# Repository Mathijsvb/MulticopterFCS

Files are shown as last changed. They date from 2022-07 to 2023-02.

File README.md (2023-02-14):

# About the project

MulticopterFCS is a flight controller build from the ground up. It is meant to be a development platform mainly focused on autonomous indoor flying of multi-rotor drones. 

> **Warning**
> The current version still contains design errors.

|Diagram|Board|
|---|---|
|DrawIO block diagrams-Pagina-5 drawio (3)|WhatsApp Image 2022-08-17 at 5 33 48 PM|

# Key features

**On board:**
* High performance MCU (STM32H743 running up to 480 MHz)
* Accelerometer and gyro (MPU6000)
* Magnetometer (HMC5883L)
* Pressure and temperature sensor (BMP388)
* 64-Kbit of F-RAM (FM24C64B)
* 2x RGB LED

**Connectors:**

| **quantity** 	| **purpose**  	| **connector type** 	| **Comment** |
|---	|---	|---	|---	|
| 1 	| SWD/JTAG 	| 1.27 mm pitch 10-pin 	| For programming and debugging 	|
| 1 	| SDIO 	| Micro SD Card 	| For logging data during the flight 	|
| 1 	| I²C 	| JST SH 4-pin 	| External I²C connector 	|
| 2 	| UART 	| JST SH 4-pin 	| External UART connector 	|
| 1 	| Battery  	| JST SH 2-pin 	| Used to measure battery voltage 	|
| 1 	| LED	  	| JST SH 8-pin 	| To control external LEDs 	|
| 1 	| IBUS 	| 2.54 mm pitch header 	| IBUS used by external receivers to communicate remote control signals |
| 6 	| PWM 	| 2.54 mm pitch header 	| PWM is used to control external ESC's 	|
| 1 	| Buzzer 	| 2.54 mm pitch header 	| For connecting a buzzer 	|
| 1 	| RPLiDAR  	| 2.50 mm MOLEX SPOX 7-pin 	| This connector will be used for the RPLiDAR 	|
| 2 	| USB 	| USB Mini B 	| USB1 goes directly to the MCU, USB2 gets converted to serial first 	|

# Roadmap:

1. ✔️ Project orientation
2. ✔️ Deciding on components
3. ✔️ Creating schematic
4. ✔️ Routing PCB
5. ✔️ Manufacturing the PCB
6.  Testing
	1. ✔️ Programming MCU
	2. ❌ Gyro/Accelerometer
		1.  ✔️ Find a the reason for to the Gyro/Accelerometer not working
		*   The MPU-6000 seems to need the ability to toggle CS which the current board does not support. Board revision is needed.
		2. Pick new Gyro/Accelerometer
	3. ❌ Magnetometer
		* Can't be detected with an I2C scanner, probably dead.
	4. Barometric pressure sensor
		1. ✔️ Check if it can be found with the I2C scanner.
		2. Check is values are sensible.
	5. ❌ On board F-RAM
		* Wrong IC choice on my part.
	6. ESC control
	7. IBUS communication
	8. Buzzer
	9. ✔️ LEDs
7. Writing drivers
	1. Gyro/Accelerometer
	2. Magnetometer
	3. Barometric pressure sensor
	4. On board F-RAM
	5. ESC control
	6. IBUS communication
	7. Buzzer and LEDs
	8. SD Card
	9. USB
8. Signal processing
	1. Data conversion and correction
	2. Data filtering
	3. Extended Kalman filter implementation for sensor fusion
	4. PI(D) controller
9. FSM controller 
10. Data logging on the SD Card

Future goals on the roadmap are likely to be Simultaneous Localization and Mapping using a LiDAR implementation. Based on this, autonomous indoor flight could be developed.

# Licensing

**This system is still a work in progress, use anything inside this repository at your own risk.**

This an open source project released under the BSD 3-Clause License.

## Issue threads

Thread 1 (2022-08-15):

Unable to communicate with the MPU6000

Mathijsvb, 2022-08-15:
The last few days I've been trying to communicate with the MPU6000 chip with no success. This chip functions as the acceleromiter and gyro of the flight controller board.

**What I've tried:**

1.  I've tried to communicate with the IC via SPI, but the MISO line remained low. I tried I²C, but no message was acknowledged.
2. I've tried replacing the IC with a new one. This yielded the same results. Do note that the chips did not arrive in their original packaging, so there is a chance that both IC's were reused and thus not as reliable.

---

**Additional info:**

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
This was recorded using a logic analyser. The first byte send starts with a 1 for MSB to indicate READ and follows with the register address 0x75 which should contain the WHO_AM_I register value which is 0x68 according to the datasheet. The figure shows nothing is returned. Attempting to read from other registers also returend nothing.
Clock frequency is 1 MHz, changing the frequency yields the same results. As for SPI settings: clock polarity is high and data is read on the second edge.

When looking at the board, the solder joints seem fine, but it is hard to judge since the joints are underneath the package.
Component values were checked and seemed fine.

Here is the schematic used. Signal lines go to the MCU unimpeded.
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

Any possible solutions or advice would be appreciated. Any feedback regarding the issue itself would also be nice, was it clear? Would you have liked additional info?

**References:**
General datasheet MPU6000: https://invensense.tdk.com/wp-content/uploads/2015/02/MPU-6000-Datasheet1.pdf
Register datasheet MPU6000: https://invensense.tdk.com/wp-content/uploads/2015/02/MPU-6000-Register-Map1.pdf
Datasheet of the MCU: https://www.st.com/resource/en/datasheet/stm32h743vi.pdf

Mathijsvb, 2022-08-18:
Update: Still no communication. What I did find was a [board that's build around MPU-6000](https://nl.rs-online.com/web/p/sensor-development-tools/8231892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) with most pins exposed. If I succeed in communicating with it, I can find out whether I'm did something wrong or if the IC's are dead.

---
At the same time, I'm looking for a suitable replacement for the MPU-6000 since it's discontinued. This is proving to be difficult since this type of IC is almost always out of stock. Some contenders:

* BNO055
* BMI088
* ISM330DHC
* LSM6DSOX
* MPU-6050 or ICM-20649 (These are discontinued as well but if availability is good they could still make sense)
* ICM-40609-D (currently in production but not yet available)

jurra, 2022-08-18:
Hi @Mathijsvb I can only give you feedback on the issue, is quite clear.

Jerzeek, 2022-08-24:
Yeah the MPU-6050 seems mostly pin compatible, but you do lose the ability for SPI communication, I don't know how important speed is. maybe pop in one of these 6050's and see if you can get i2c communication working. then you know if it is the board or the chip

Mathijsvb, 2022-08-29:
Hi @Jerzeek, thank you for the response. It's a good suggestion, and I would have been able to do this if I had not grounded the CS pin on the MPU-6000. This prevents being able to supply VLOGIC on the MPU-6050 (both pin 8 in the diagram). If I decide to use one of these, I'll definitely change this in a future revision of the board.

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

Mathijsvb, 2023-02-14:
I'm back with an update. Attaching the [MPU-6000 based dev board](https://nl.rs-online.com/web/p/sensor-development-tools/8231892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) discussed previously to the flight controller still yielded the same results of being unable to read out the WHO_AM_I register. So I took an entirely different microcontroller and attempted to read out the WHO_AM_I register again and it worked!

The difference between the two setups was that my test setup had a controllable CS pin, while the one in the flight controller was standard connected to ground. So what happens if we pull CS in the test setup standard low? Well, no response (and sometimes a gibberish response).

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

Searching around, it seems that some SPI devices need the CS transition to successfully manage communication and some don't. My best guess is that toggling CS is required for communication to remain in sync for the MPU-6000 (I was unable to find this detail in the datasheet, however). I'll close the issue for now.

This means a new board will need to be designed eventually after the other functionalities are tested.

Closed 2023-02-14.

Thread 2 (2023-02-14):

Improvements for the next board iteration

Mathijsvb, 2023-02-14:
In this issue, I'd like to compile all the known mistakes in the V1.0 board
1. No control over the MPU-6000 CS pin disallowing any form of communication over SPI (Or the ability to switch to I2C)
2. The FM24C64B works on 5V which I somehow completely missed and connected to the 3.3V supply

The future revision will contain:
1. A different gyro and accelerometer that is available

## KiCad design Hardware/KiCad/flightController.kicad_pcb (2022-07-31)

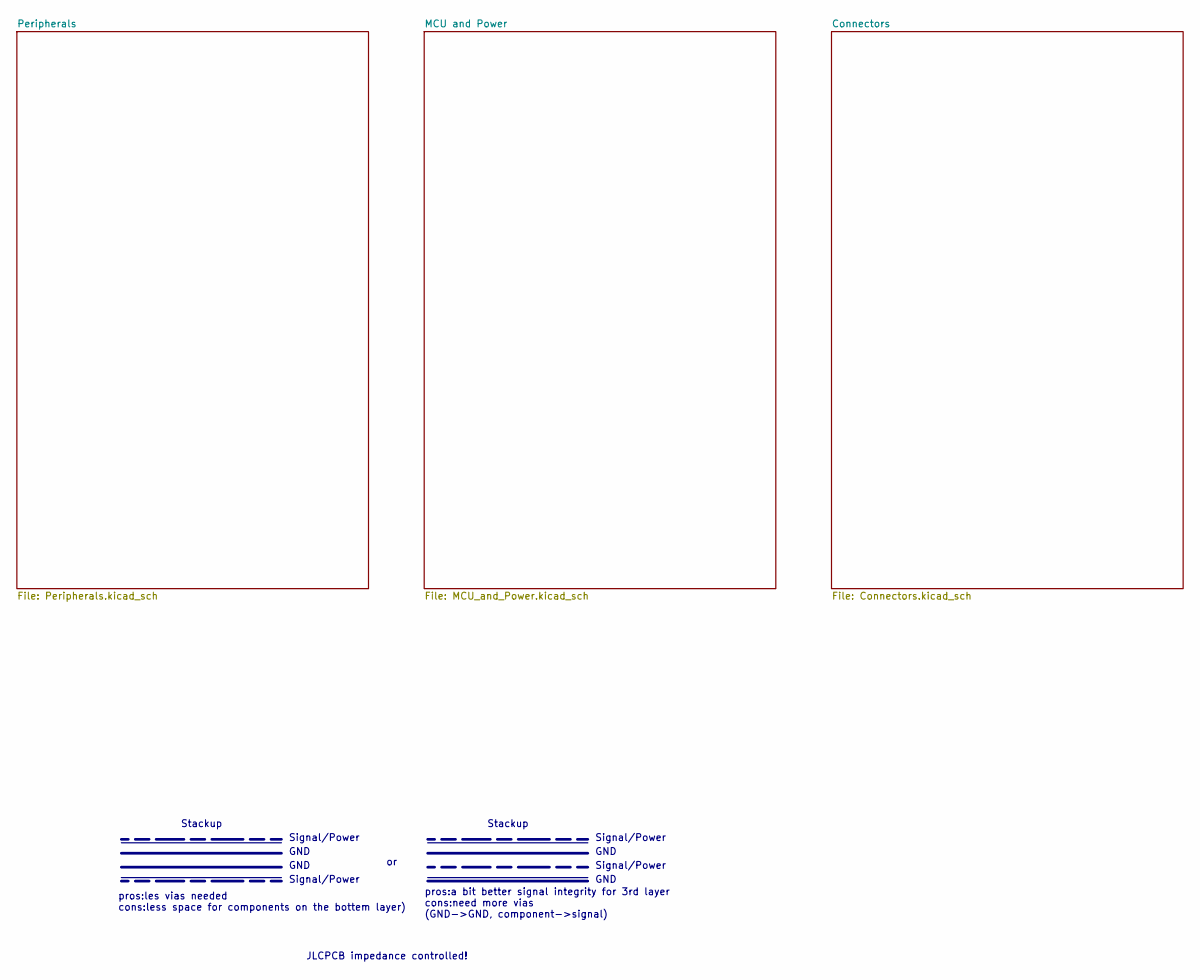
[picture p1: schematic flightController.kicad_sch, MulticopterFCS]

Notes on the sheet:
GND
Stackup
pros:les vias needed cons:less space for components on the bottem layer)
JLCPCB impedance controlled!
pros:a bit better signal integrity for 3rd layer cons:need more vias (GND->GND, component->signal)
Signal/Power

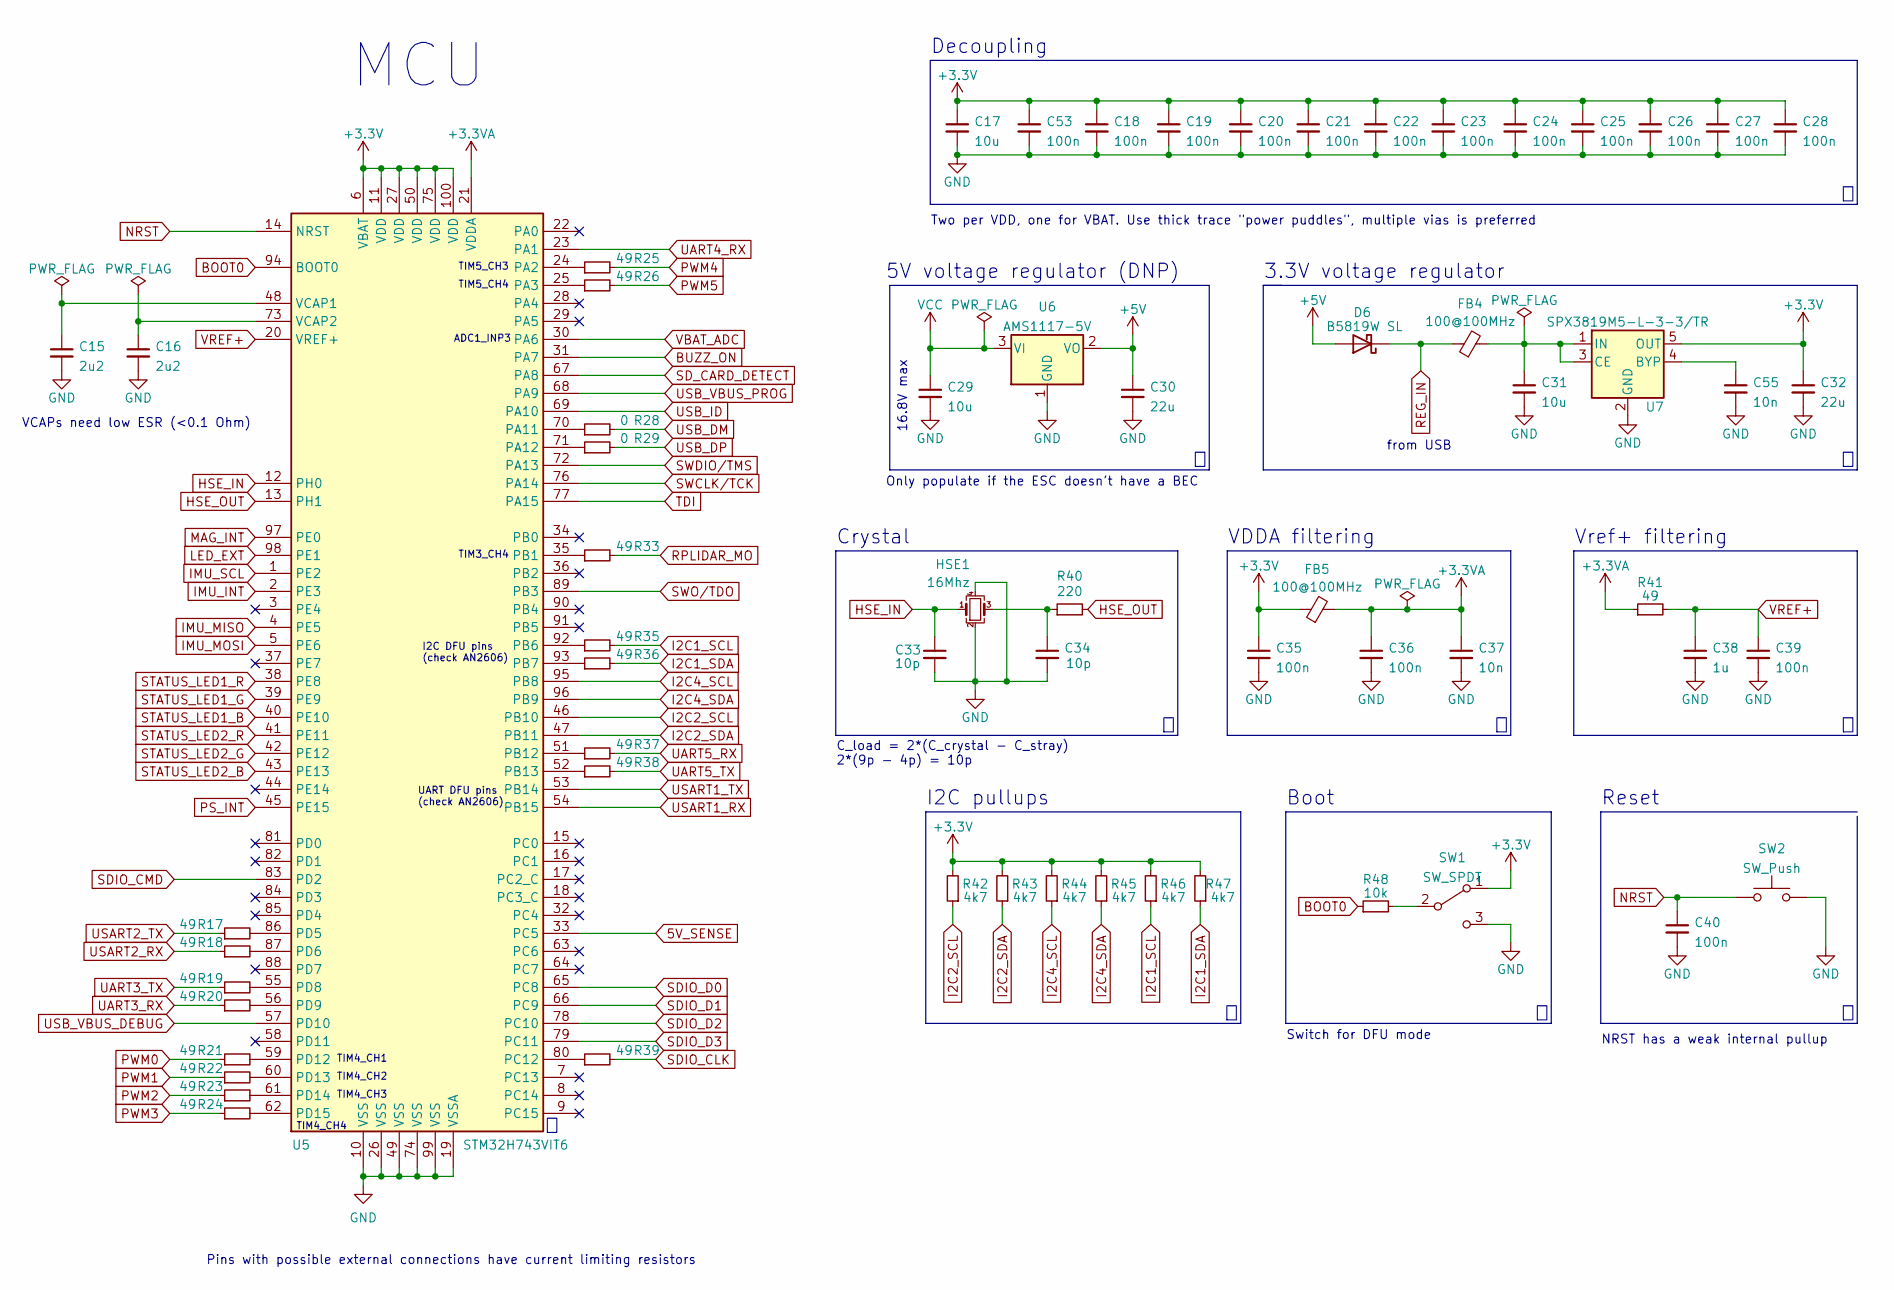
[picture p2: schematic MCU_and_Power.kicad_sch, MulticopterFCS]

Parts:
C15, C16: 2u2; C_0402_1005Metric; JLCPCB Part# C12530
C17, C29, C31: 10u; C_0603_1608Metric; JLCPCB Part# C96446
C18, C19, C20, C21, C22, C23, C24, C25, C26, C27, C28, C35, C36, C39, C40, C53: 100n; C_0402_1005Metric; JLCPCB Part# C1525
C30, C32: 22u; C_0603_1608Metric; JLCPCB Part# C59461
C33, C34: 10p; C_0402_1005Metric; JLCPCB Part# C32949
C37, C55: 10n; C_0402_1005Metric; JLCPCB Part# C15195
C38: 1u; C_0603_1608Metric; JLCPCB Part# C15849
D6: B5819W SL; D_SOD-123; JLCPCB Part# C8598
FB4, FB5: 100@100MHz; L_0603_1608Metric; JLCPCB Part# DNP
HSE1: 16Mhz; Crystal_SMD_3225-4Pin_3.2x2.5mm; JLCPCB Part# C13738
R17, R18, R19, R20, R21, R22, R23, R24, R25, R26, R33, R35, R36, R37, R38, R39, R41: 49; R_0402_1005Metric
R28, R29: 0; R_0402_1005Metric
R40: 220; R_0402_1005Metric
R42, R43, R44, R45, R46, R47: 4k7; R_0402_1005Metric
R48: 10k; R_0402_1005Metric
SW1: SW_SPDT; SW_SPDT_PCM12; JLCPCB Part# DNP
SW2: SW_Push; SW_SPST_FSMSM; JLCPCB Part# DNP
U5: STM32H743VIT6; LQFP-100_14x14mm_P0.5mm; JLCPCB Part# DNP
U6: AMS1117-5V; SOT-223-3_TabPin2; JLCPCB Part# DNP
U7: SPX3819M5-L-3-3/TR; SOT-23-5; JLCPCB Part# DNP

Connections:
5V_SENSE: U5.33 (PC5); also elsewhere on the board
+3.3VA: C36.1, C37.1, FB5.2, R41.1, U5.21 (VDDA)
+3V3: C17.1, C18.1, C19.1, C20.1, C21.1, C22.1, C23.1, C24.1, C25.1, C26.1, C27.1, C28.1, C32.1, C35.1, C53.1, FB5.1, R42.2, R43.2, R44.2, R45.2, R46.2, R47.2, SW1.1 (A), U5.6 (VBAT), U5.11 (VDD), U5.27 (VDD), U5.50 (VDD), U5.75 (VDD), U5.100 (VDD), U7.5 (OUT); also elsewhere on the board
+5V: C30.1, D6.2 (A), U6.2 (VO); also elsewhere on the board
BOOT0: R48.1, U5.94 (BOOT0)
BUZZ_ON: U5.31 (PA7); also elsewhere on the board
GND: C15.2, C16.2, C17.2, C18.2, C19.2, C20.2, C21.2, C22.2, C23.2, C24.2, C25.2, C26.2, C27.2, C28.2, C29.2, C30.2, C31.2, C32.2, C33.2, C34.2, C35.2, C36.2, C37.2, C38.2, C39.2, C40.2, C53.2, C55.2, HSE1.2, HSE1.4, SW1.3 (C), SW2.2, U5.10 (VSS), U5.19 (VSSA), U5.26 (VSS), U5.49 (VSS), U5.74 (VSS), U5.99 (VSS), U6.1 (GND), U7.2 (GND); also elsewhere on the board
HSE_IN: C33.1, HSE1.1, U5.12 (PH0)
HSE_OUT: R40.2, U5.13 (PH1)
I2C1_SCL: R35.2, R46.1; also elsewhere on the board
I2C1_SDA: R36.2, R47.1; also elsewhere on the board
I2C2_SCL: R42.1, U5.46 (PB10); also elsewhere on the board
I2C2_SDA: R43.1, U5.47 (PB11); also elsewhere on the board
I2C4_SCL: R44.1, U5.95 (PB8); also elsewhere on the board
I2C4_SDA: R45.1, U5.96 (PB9); also elsewhere on the board
IMU_INT: U5.2 (PE3); also elsewhere on the board
IMU_MISO: U5.4 (PE5); also elsewhere on the board
IMU_MOSI: U5.5 (PE6); also elsewhere on the board
IMU_SCL: U5.1 (PE2); also elsewhere on the board
LED_EXT: U5.98 (PE1); also elsewhere on the board
MAG_INT: U5.97 (PE0); also elsewhere on the board
NRST: C40.1, SW2.1, U5.14 (NRST); also elsewhere on the board
unnamed: C15.1, U5.48 (VCAP1)
unnamed: C16.1, U5.73 (VCAP2)
unnamed: C31.1, FB4.2, U7.1 (IN), U7.3 (CE)
unnamed: C34.1, HSE1.3, R40.1
unnamed: C55.1, U7.4 (BYP)
unnamed: R17.2, U5.86 (PD5)
unnamed: R18.2, U5.87 (PD6)
unnamed: R19.2, U5.55 (PD8)
unnamed: R20.2, U5.56 (PD9)
unnamed: R21.2, U5.59 (PD12)
unnamed: R22.2, U5.60 (PD13)
unnamed: R23.2, U5.61 (PD14)
unnamed: R24.2, U5.62 (PD15)
unnamed: R25.1, U5.24 (PA2)
unnamed: R26.1, U5.25 (PA3)
unnamed: R28.1, U5.70 (PA11)
unnamed: R29.1, U5.71 (PA12)
unnamed: R33.1, U5.35 (PB1)
unnamed: R35.1, U5.92 (PB6)
unnamed: R36.1, U5.93 (PB7)
unnamed: R37.1, U5.51 (PB12)
unnamed: R38.1, U5.52 (PB13)
unnamed: R39.1, U5.80 (PC12)
unnamed: R48.2, SW1.2 (B)
PS_INT: U5.45 (PE15); also elsewhere on the board
PWM0: R21.1; also elsewhere on the board
PWM1: R22.1; also elsewhere on the board
PWM2: R23.1; also elsewhere on the board
PWM3: R24.1; also elsewhere on the board
PWM4: R25.2; also elsewhere on the board
PWM5: R26.2; also elsewhere on the board
REG_IN: D6.1 (K), FB4.1; also elsewhere on the board
RPLIDAR_MO: R33.2; also elsewhere on the board
SDIO_CLK: R39.2; also elsewhere on the board
SDIO_CMD: U5.83 (PD2); also elsewhere on the board
SDIO_D0: U5.65 (PC8); also elsewhere on the board
SDIO_D1: U5.66 (PC9); also elsewhere on the board
SDIO_D2: U5.78 (PC10); also elsewhere on the board
SDIO_D3: U5.79 (PC11); also elsewhere on the board
SD_CARD_DETECT: U5.67 (PA8); also elsewhere on the board
STATUS_LED1_B: U5.40 (PE10); also elsewhere on the board
STATUS_LED1_G: U5.39 (PE9); also elsewhere on the board
STATUS_LED1_R: U5.38 (PE8); also elsewhere on the board
STATUS_LED2_B: U5.43 (PE13); also elsewhere on the board
STATUS_LED2_G: U5.42 (PE12); also elsewhere on the board
STATUS_LED2_R: U5.41 (PE11); also elsewhere on the board
SWCLK/TCK: U5.76 (PA14); also elsewhere on the board
SWDIO/TMS: U5.72 (PA13); also elsewhere on the board
SWO/TDO: U5.89 (PB3); also elsewhere on the board
TDI: U5.77 (PA15); also elsewhere on the board
UART3_RX: R20.1; also elsewhere on the board
UART3_TX: R19.1; also elsewhere on the board
UART4_RX: U5.23 (PA1); also elsewhere on the board
UART5_RX: R37.2; also elsewhere on the board
UART5_TX: R38.2; also elsewhere on the board
USART1_RX: U5.54 (PB15); also elsewhere on the board
USART1_TX: U5.53 (PB14); also elsewhere on the board
USART2_RX: R18.1; also elsewhere on the board
USART2_TX: R17.1; also elsewhere on the board
USB_DM: R28.2; also elsewhere on the board
USB_DP: R29.2; also elsewhere on the board
USB_ID: U5.69 (PA10); also elsewhere on the board
USB_VBUS_DEBUG: U5.57 (PD10); also elsewhere on the board
USB_VBUS_PROG: U5.68 (PA9); also elsewhere on the board
VBAT_ADC: U5.30 (PA6); also elsewhere on the board
VCC: C29.1, U6.3 (VI); also elsewhere on the board
VREF+: C38.1, C39.1, R41.2, U5.20 (VREF+)

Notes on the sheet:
Boot
Reset
ADC1_INP3
TIM5_CH3
from USB
3.3V voltage regulator
TIM4_CH3
Vref+ filtering
Pins with possible external connections have current limiting resistors
5V voltage regulator (DNP)
UART DFU pins (check AN2606)
VCAPs need low ESR (<0.1 Ohm)
VDDA filtering
Decoupling
16.8V max
I2C pullups
TIM4_CH4
NRST has a weak internal pullup
Crystal
TIM4_CH2
TIM4_CH1
MCU
Two per VDD, one for VBAT. Use thick trace "power puddles", multiple vias is preferred
I2C DFU pins (check AN2606)
Switch for DFU mode
TIM5_CH4
Only populate if the ESC doesn't have a BEC
C_load = 2*(C_crystal - C_stray) 2*(9p - 4p) = 10p
TIM3_CH4

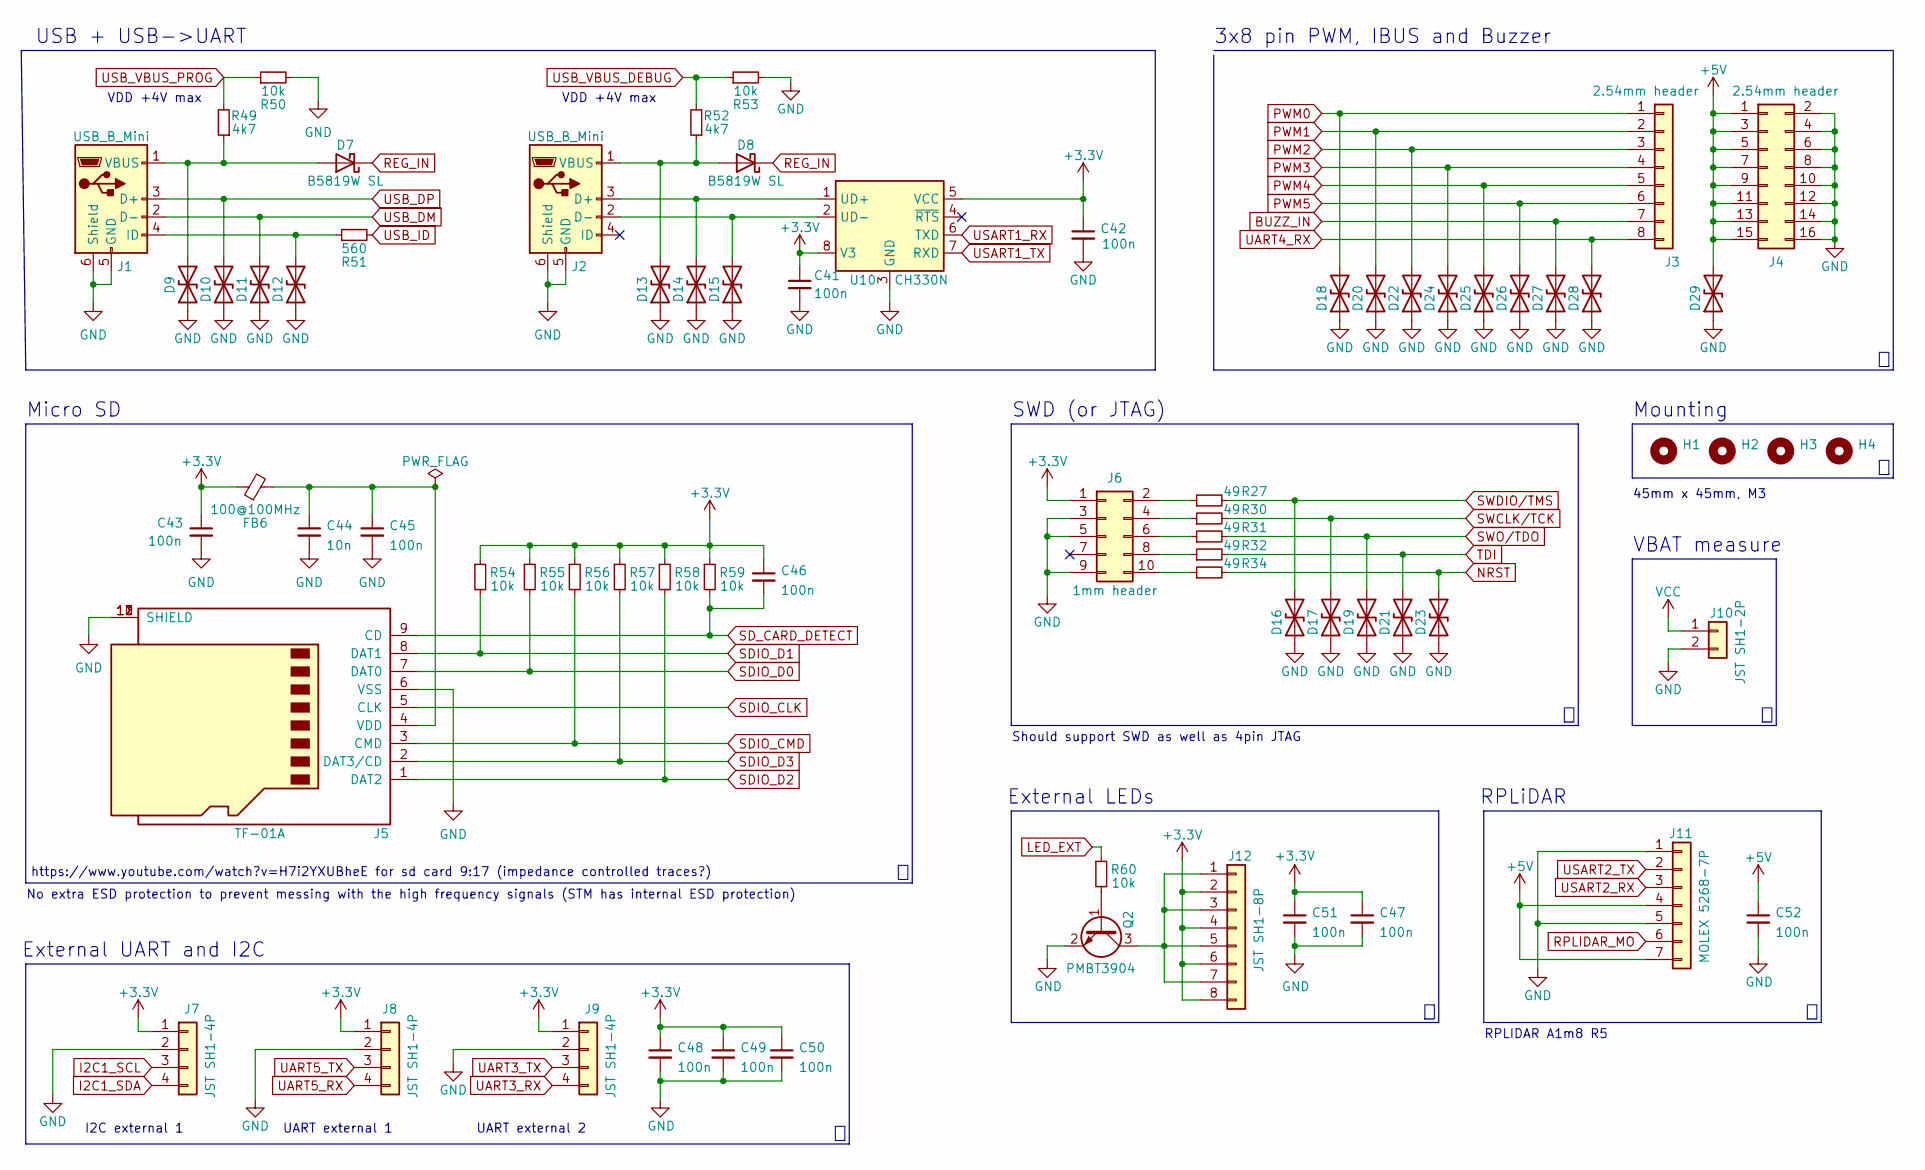
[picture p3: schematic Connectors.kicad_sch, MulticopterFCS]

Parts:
C41, C42, C43, C45, C46, C47, C48, C49, C50, C51, C52: 100n; C_0402_1005Metric; JLCPCB Part# C1525
C44: 10n; C_0402_1005Metric; JLCPCB Part# C15195
D7, D8: B5819W SL; D_SOD-123; JLCPCB Part# C8598
D9, D10, D11, D12, D13, D14, D15, D16, D17, D18, D19, D20, D21, D22, D23, D24, D25, D26, D27, D28, D29: LXES15AAA1-133; R_0402_1005Metric
FB6: 100@100MHz; L_0603_1608Metric; JLCPCB Part# DNP
H1, H2, H3, H4: MountingHole; MountingHole_3.2mm_M3_ISO14580_Pad; JLCPCB Part# DNP
J1, J2: USB_B_Mini; USB_Mini-B_Wuerth_65100516121_Horizontal; JLCPCB Part# DNP
J3: 2.54mm header; PinHeader_1x08_P2.54mm_Vertical_lessSilk; JLCPCB Part# DNP
J4: 2.54mm header; PinHeader_2x08_P2.54mm_Horizontal_lessSilk; JLCPCB Part# DNP
J5: TF-01A; JLCPCB Part# DNP
J6: 1mm header; PinHeader_2x05_P1.27mm_Vertical_SMD; JLCPCB Part# DNP
J7, J8, J9: JST SH1-4P; JST_SH_SM04B-SRSS-TB_1x04-1MP_P1.00mm_Horizontal; JLCPCB Part# DNP
J10: JST SH1-2P; JST_SHL_SM02B-SHLS-TF_1x02-1MP_P1.00mm_Horizontal; JLCPCB Part# DNP
J11: MOLEX 5268-7P; Molex_SPOX_5268-07A_1x07_P2.50mm_Horizontal; JLCPCB Part# DNP
J12: JST SH1-8P; JST_SH_SM08B-SRSS-TB_1x08-1MP_P1.00mm_Horizontal; JLCPCB Part# DNP
Q2: PMBT3904; SOT-23; JLCPCB Part# DNP
R27, R30, R31, R32, R34: 49; R_0402_1005Metric
R49, R52: 4k7; R_0402_1005Metric
R50, R53, R54, R55, R56, R57, R58, R59, R60: 10k; R_0402_1005Metric
R51: 560; R_0402_1005Metric
U10: CH330N; SOP-8_3.9x4.9mm_P1.27mm; JLCPCB Part# C108996

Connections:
+3V3: C41.1, C42.1, C43.1, C46.1, C47.1, C48.1, C49.1, C50.1, C51.1, FB6.1, J6.1, J7.1, J8.1, J9.1, J12.2, J12.4, J12.6, J12.8, R54.1, R55.1, R56.1, R57.1, R58.1, R59.1, U10.5 (VCC), U10.8 (V3); also elsewhere on the board
+5V: C52.1, D29.2 (A2), J4.1, J4.3, J4.5, J4.7, J4.9, J4.11, J4.13, J4.15, J11.4, J11.7; also elsewhere on the board
BUZZ_IN: D27.2 (A2), J3.7; also elsewhere on the board
GND: C41.2, C42.2, C43.2, C44.2, C45.2, C47.2, C48.2, C49.2, C50.2, C51.2, C52.2, D9.1 (A1), D10.1 (A1), D11.1 (A1), D12.1 (A1), D13.1 (A1), D14.1 (A1), D15.1 (A1), D16.1 (A1), D17.1 (A1), D18.1 (A1), D19.1 (A1), D20.1 (A1), D21.1 (A1), D22.1 (A1), D23.1 (A1), D24.1 (A1), D25.1 (A1), D26.1 (A1), D27.1 (A1), D28.1 (A1), D29.1 (A1), J1.5 (GND), J1.6 (Shield), J2.5 (GND), J2.6 (Shield), J4.2, J4.4, J4.6, J4.8, J4.10, J4.12, J4.14, J4.16, J5.6 (VSS), J5.10 (SHIELD), J5.11 (SHIELD), J5.12 (SHIELD), J5.13 (SHIELD), J6.3, J6.5, J6.9, J7.2, J8.2, J9.2, J10.2, J11.1, J11.5, Q2.2 (E), R50.2, R53.2, U10.3 (GND); also elsewhere on the board
I2C1_SCL: J7.3; also elsewhere on the board
I2C1_SDA: J7.4; also elsewhere on the board
LED_EXT: R60.1; also elsewhere on the board
NRST: D23.2 (A2), R34.2; also elsewhere on the board
unnamed: C44.1, C45.1, FB6.2, J5.4 (VDD)
unnamed: D7.2 (A), D9.2 (A2), J1.1 (VBUS), R49.1
unnamed: D8.2 (A), D13.2 (A2), J2.1 (VBUS), R52.1
unnamed: D12.2 (A2), J1.4 (ID), R51.1
unnamed: D15.2 (A2), J2.2 (D-), U10.2 (UD-)
unnamed: D14.2 (A2), J2.3 (D+), U10.1 (UD+)
unnamed: J6.2, R27.1
unnamed: J6.4, R30.1
unnamed: J6.6, R31.1
unnamed: J6.8, R32.1
unnamed: J6.10, R34.1
unnamed: J12.1, J12.3, J12.5, J12.7, Q2.3 (C)
unnamed: Q2.1 (B), R60.2
PWM0: D18.2 (A2), J3.1; also elsewhere on the board
PWM1: D20.2 (A2), J3.2; also elsewhere on the board
PWM2: D22.2 (A2), J3.3; also elsewhere on the board
PWM3: D24.2 (A2), J3.4; also elsewhere on the board
PWM4: D25.2 (A2), J3.5; also elsewhere on the board
PWM5: D26.2 (A2), J3.6; also elsewhere on the board
REG_IN: D7.1 (K), D8.1 (K); also elsewhere on the board
RPLIDAR_MO: J11.6; also elsewhere on the board
SDIO_CLK: J5.5 (CLK); also elsewhere on the board
SDIO_CMD: J5.3 (CMD), R56.2; also elsewhere on the board
SDIO_D0: J5.7 (DAT0), R55.2; also elsewhere on the board
SDIO_D1: J5.8 (DAT1), R54.2; also elsewhere on the board
SDIO_D2: J5.1 (DAT2), R58.2; also elsewhere on the board
SDIO_D3: J5.2 (DAT3/CD), R57.2; also elsewhere on the board
SD_CARD_DETECT: C46.2, J5.9 (CD), R59.2; also elsewhere on the board
SWCLK/TCK: D17.2 (A2), R30.2; also elsewhere on the board
SWDIO/TMS: D16.2 (A2), R27.2; also elsewhere on the board
SWO/TDO: D19.2 (A2), R31.2; also elsewhere on the board
TDI: D21.2 (A2), R32.2; also elsewhere on the board
UART3_RX: J9.4; also elsewhere on the board
UART3_TX: J9.3; also elsewhere on the board
UART4_RX: D28.2 (A2), J3.8; also elsewhere on the board
UART5_RX: J8.4; also elsewhere on the board
UART5_TX: J8.3; also elsewhere on the board
USART1_RX: U10.6 (TXD); also elsewhere on the board
USART1_TX: U10.7 (RXD); also elsewhere on the board
USART2_RX: J11.3; also elsewhere on the board
USART2_TX: J11.2; also elsewhere on the board
USB_DM: D11.2 (A2), J1.2 (D-); also elsewhere on the board
USB_DP: D10.2 (A2), J1.3 (D+); also elsewhere on the board
USB_ID: R51.2; also elsewhere on the board
USB_VBUS_DEBUG: R52.2, R53.1; also elsewhere on the board
USB_VBUS_PROG: R49.2, R50.1; also elsewhere on the board
VCC: J10.1; also elsewhere on the board

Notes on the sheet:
https://www.youtube.com/watch?v=H7i2YXUBheE for sd card 9:17 (impedance controlled traces?)
RPLiDAR
Mounting
External LEDs
UART external 2
External UART and I2C
Micro SD
VDD +4V max
3x8 pin PWM, IBUS and Buzzer
No extra ESD protection to prevent messing with the high frequency signals (STM has internal ESD protection)
I2C external 1
45mm x 45mm, M3
RPLIDAR A1m8 R5
Should support SWD as well as 4pin JTAG
VBAT measure
SWD (or JTAG)
USB + USB->UART
UART external 1

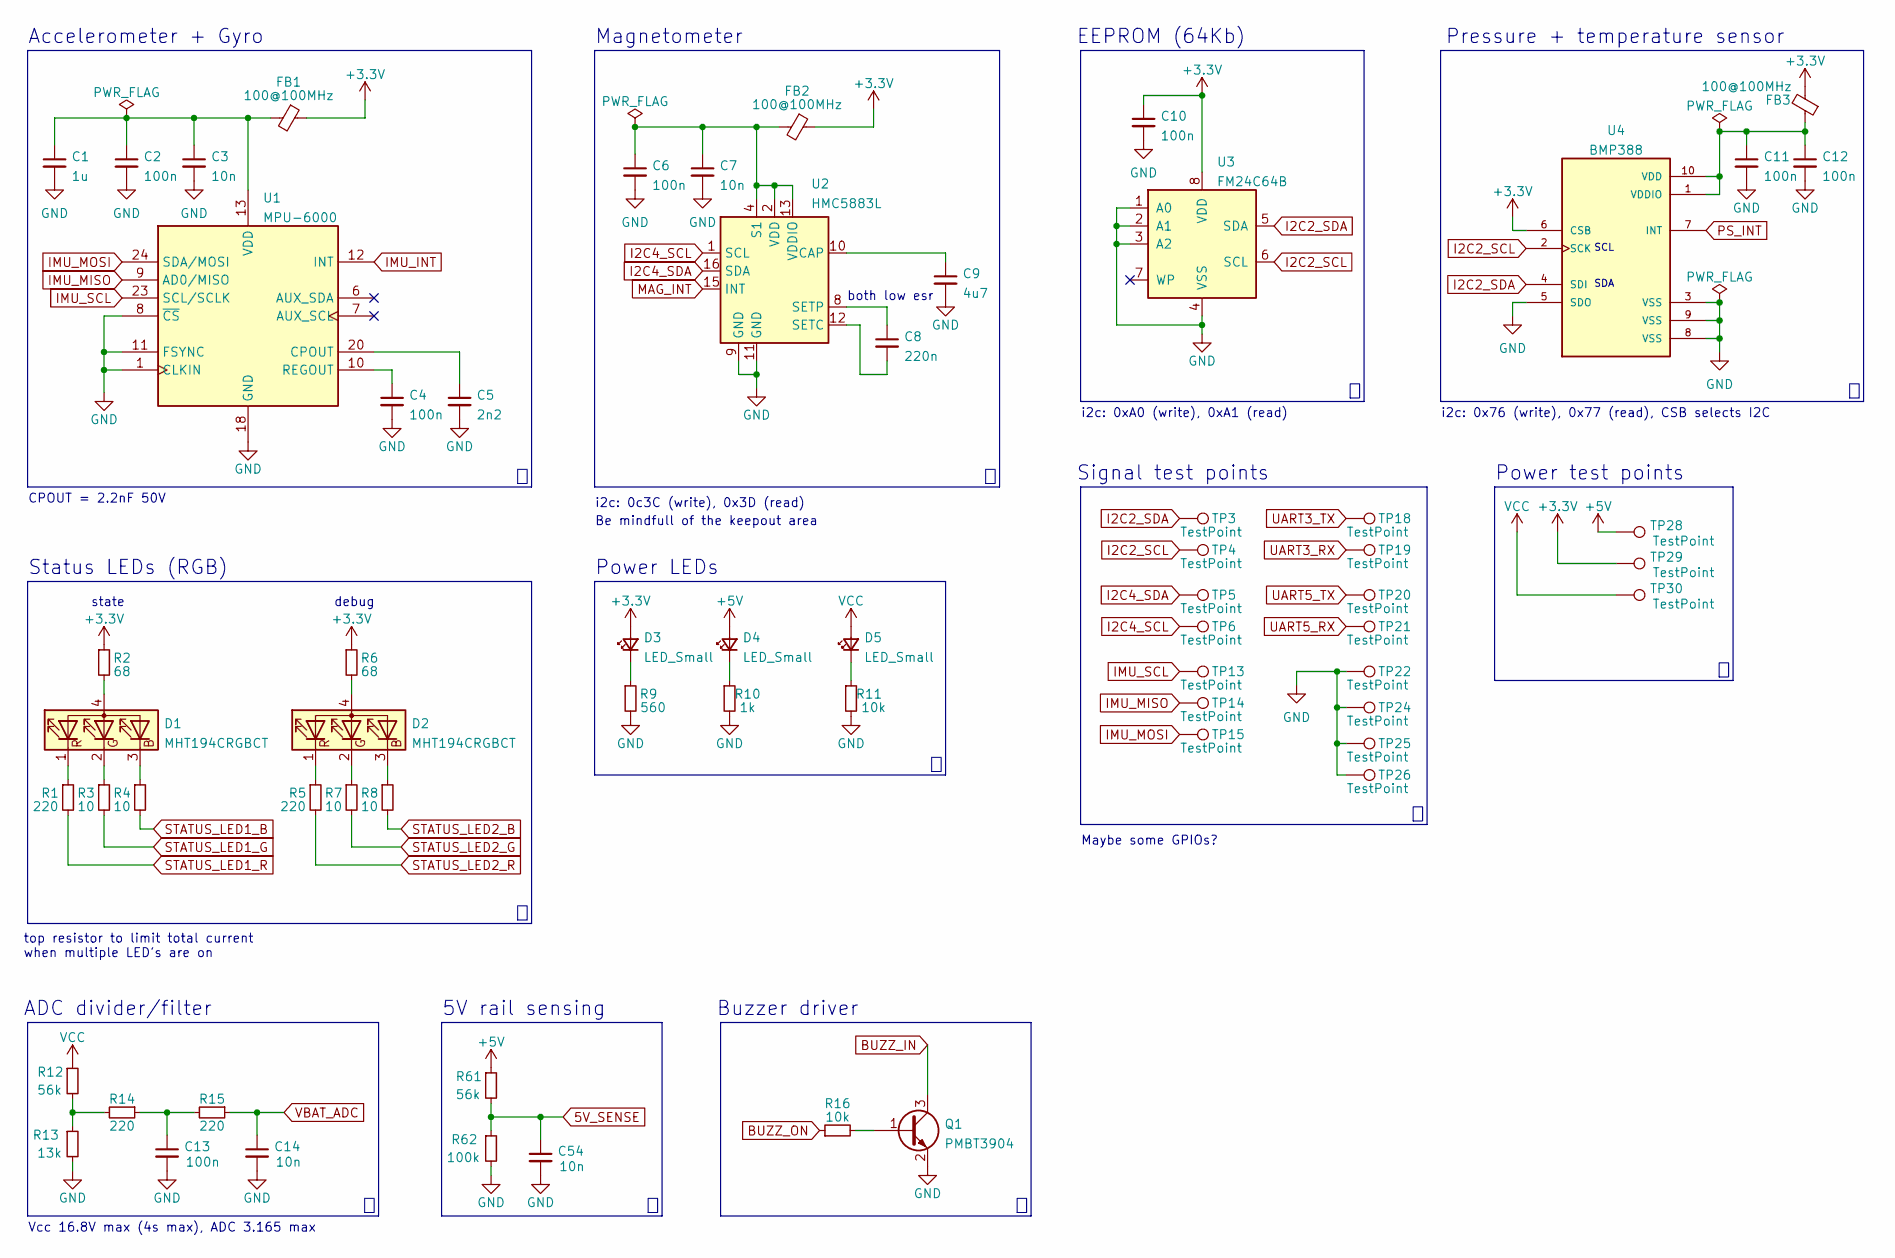
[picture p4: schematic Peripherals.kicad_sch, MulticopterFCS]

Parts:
C1: 1u; C_0603_1608Metric; JLCPCB Part# C15849
C2, C4, C6, C10, C11, C12, C13: 100n; C_0402_1005Metric; JLCPCB Part# C1525
C3, C7, C14, C54: 10n; C_0402_1005Metric; JLCPCB Part# C15195
C5: 2n2; C_0402_1005Metric; JLCPCB Part# C1531
C8: 220n; C_0603_1608Metric; JLCPCB Part# C21120
C9: 4u7; C_0603_1608Metric; JLCPCB Part# C19666
D1, D2: MHT194CRGBCT; 0605; JLCPCB Part# DNP
D3, D4, D5: LED_Small; LED_0603_1608Metric; JLCPCB Part# DNP
FB1, FB2, FB3: 100@100MHz; L_0603_1608Metric; JLCPCB Part# DNP
Q1: PMBT3904; SOT-23; JLCPCB Part# DNP
R1, R5, R14, R15: 220; R_0402_1005Metric
R2, R6: 68; R_0603_1608Metric
R3, R4, R7, R8: 10; R_0402_1005Metric
R9: 560; R_0603_1608Metric
R10: 1k; R_0603_1608Metric
R11: 10k; R_0603_1608Metric
R12, R61: 56k; R_0402_1005Metric
R13: 13k; R_0402_1005Metric
R16: 10k; R_0402_1005Metric
R62: 100k; R_0402_1005Metric
TP3, TP4, TP5, TP6, TP13, TP14, TP15, TP18, TP19, TP20, TP21, TP22, TP24, TP25, TP26, TP28, TP29, TP30: TestPoint; TestPoint_Pad_D1.0mm; JLCPCB Part# DNP
U1: MPU-6000; InvenSense_QFN-24_4x4mm_P0.5mm; JLCPCB Part# DNP
U2: HMC5883L; LGA-16_3x3mm_P0.5mm_Large_Pads; JLCPCB Part# DNP
U3: FM24C64B; SOIC-8_3.9x4.9mm_P1.27mm; JLCPCB Part# DNP
U4: BMP388; PQFN50P200X200X80-10N; JLCPCB Part# C779278

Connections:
5V_SENSE: C54.1, R61.2, R62.1; also elsewhere on the board
+3V3: C10.1, D3.2 (A), FB1.1, FB2.1, FB3.2, R2.1, R6.1, TP29.1, U3.8 (VDD), U4.6 (CSB); also elsewhere on the board
+5V: D4.2 (A), R61.1, TP28.1; also elsewhere on the board
BUZZ_IN: Q1.3 (C); also elsewhere on the board
BUZZ_ON: R16.1; also elsewhere on the board
GND: C1.2, C2.2, C3.2, C4.2, C5.2, C6.2, C7.2, C9.2, C10.2, C11.2, C12.2, C13.2, C14.2, C54.2, Q1.2 (E), R9.2, R10.2, R11.2, R13.2, R62.2, TP22.1, TP24.1, TP25.1, TP26.1, U1.1 (CLKIN), U1.8 (~CS), U1.11 (FSYNC), U1.18 (GND), U2.9 (GND), U2.11 (GND), U3.1 (A0), U3.2 (A1), U3.3 (A2), U3.4 (VSS), U4.3 (VSS), U4.5 (SDO), U4.8 (VSS), U4.9 (VSS); also elsewhere on the board
I2C2_SCL: TP4.1, U3.6 (SCL), U4.2 (SCK); also elsewhere on the board
I2C2_SDA: TP3.1, U3.5 (SDA), U4.4 (SDI); also elsewhere on the board
I2C4_SCL: TP6.1, U2.1 (SCL); also elsewhere on the board
I2C4_SDA: TP5.1, U2.16 (SDA); also elsewhere on the board
IMU_INT: U1.12 (INT); also elsewhere on the board
IMU_MISO: TP14.1, U1.9 (AD0/MISO); also elsewhere on the board
IMU_MOSI: TP15.1, U1.24 (SDA/MOSI); also elsewhere on the board
IMU_SCL: TP13.1, U1.23 (SCL/SCLK); also elsewhere on the board
MAG_INT: U2.15 (INT); also elsewhere on the board
unnamed: C1.1, C2.1, C3.1, FB1.2, U1.13 (VDD)
unnamed: C4.1, U1.10 (REGOUT)
unnamed: C5.1, U1.20 (CPOUT)
unnamed: C6.1, C7.1, FB2.2, U2.2 (VDD), U2.4 (S1), U2.13 (VDDIO)
unnamed: C8.1, U2.8 (SETP)
unnamed: C8.2, U2.12 (SETC)
unnamed: C9.1, U2.10 (CAP)
unnamed: C11.1, C12.1, FB3.1, U4.1 (VDDIO), U4.10 (VDD)
unnamed: C13.1, R14.1, R15.2
unnamed: D1.1 (RK), R1.1
unnamed: D1.2 (GK), R3.1
unnamed: D1.3 (BK), R4.1
unnamed: D1.4 (A), R2.2
unnamed: D2.1 (RK), R5.1
unnamed: D2.2 (GK), R7.1
unnamed: D2.3 (BK), R8.1
unnamed: D2.4 (A), R6.2
unnamed: D3.1 (K), R9.1
unnamed: D4.1 (K), R10.1
unnamed: D5.1 (K), R11.1
unnamed: Q1.1 (B), R16.2
unnamed: R12.2, R13.1, R14.2
PS_INT: U4.7 (INT); also elsewhere on the board
STATUS_LED1_B: R4.2; also elsewhere on the board
STATUS_LED1_G: R3.2; also elsewhere on the board
STATUS_LED1_R: R1.2; also elsewhere on the board
STATUS_LED2_B: R8.2; also elsewhere on the board
STATUS_LED2_G: R7.2; also elsewhere on the board
STATUS_LED2_R: R5.2; also elsewhere on the board
UART3_RX: TP19.1; also elsewhere on the board
UART3_TX: TP18.1; also elsewhere on the board
UART5_RX: TP21.1; also elsewhere on the board
UART5_TX: TP20.1; also elsewhere on the board
VBAT_ADC: C14.1, R15.1; also elsewhere on the board
VCC: D5.2 (A), R12.1, TP30.1; also elsewhere on the board

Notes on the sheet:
SCL
ADC divider/filter
5V rail sensing
Signal test points
Buzzer driver
top resistor to limit total current when multiple LED's are on
Power LEDs
Maybe some GPIOs?
i2c: 0x76 (write), 0x77 (read), CSB selects I2C
Magnetometer
SDA
both low esr
EEPROM (64Kb)
i2c: 0c3C (write), 0x3D (read)
debug
i2c: 0xA0 (write), 0xA1 (read)
CPOUT = 2.2nF 50V
Pressure + temperature sensor
Be mindfull of the keepout area
Status LEDs (RGB)
Accelerometer + Gyro
Vcc 16.8V max (4s max), ADC 3.165 max
Power test points
state

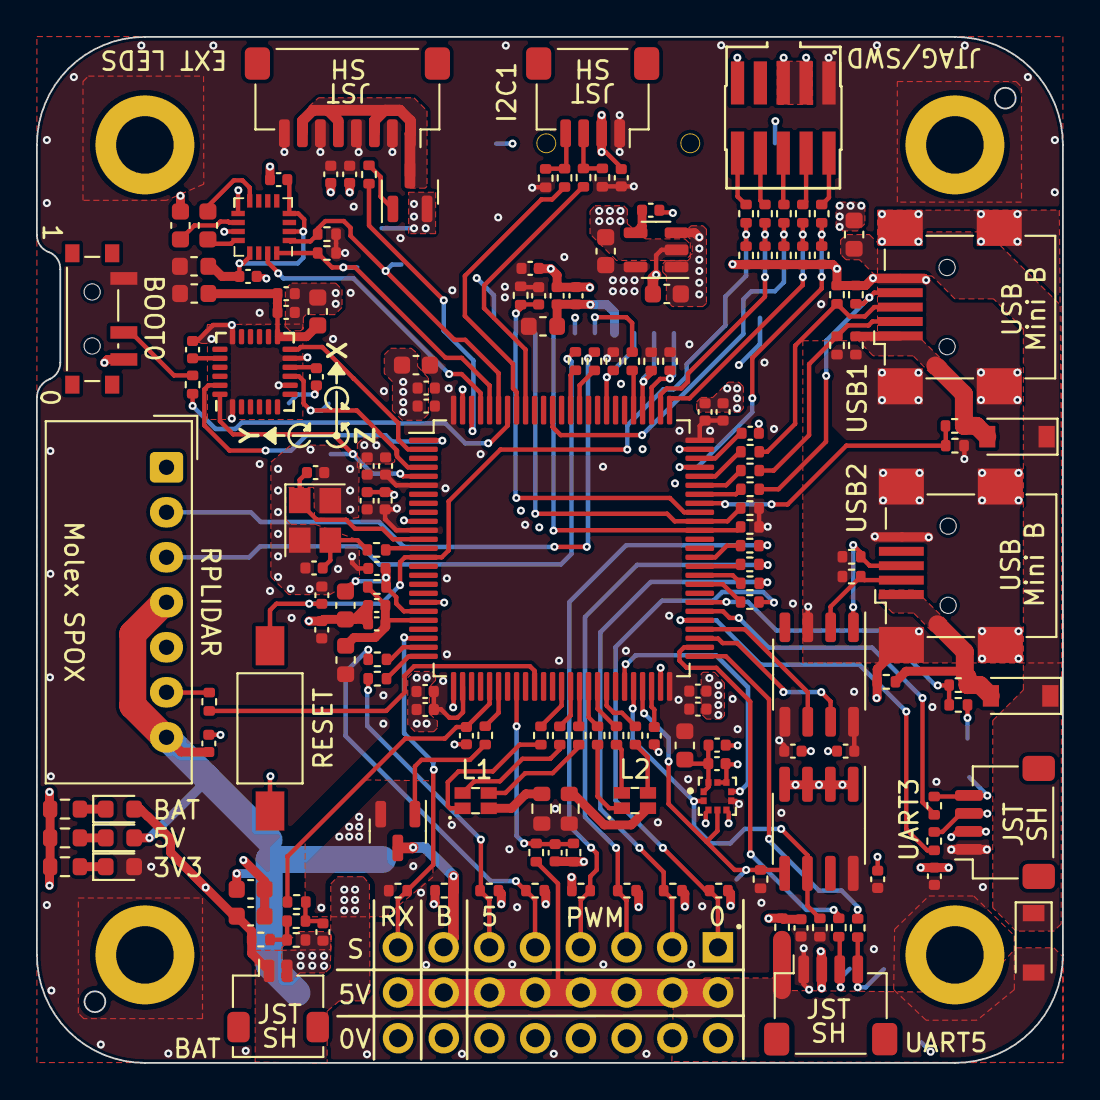
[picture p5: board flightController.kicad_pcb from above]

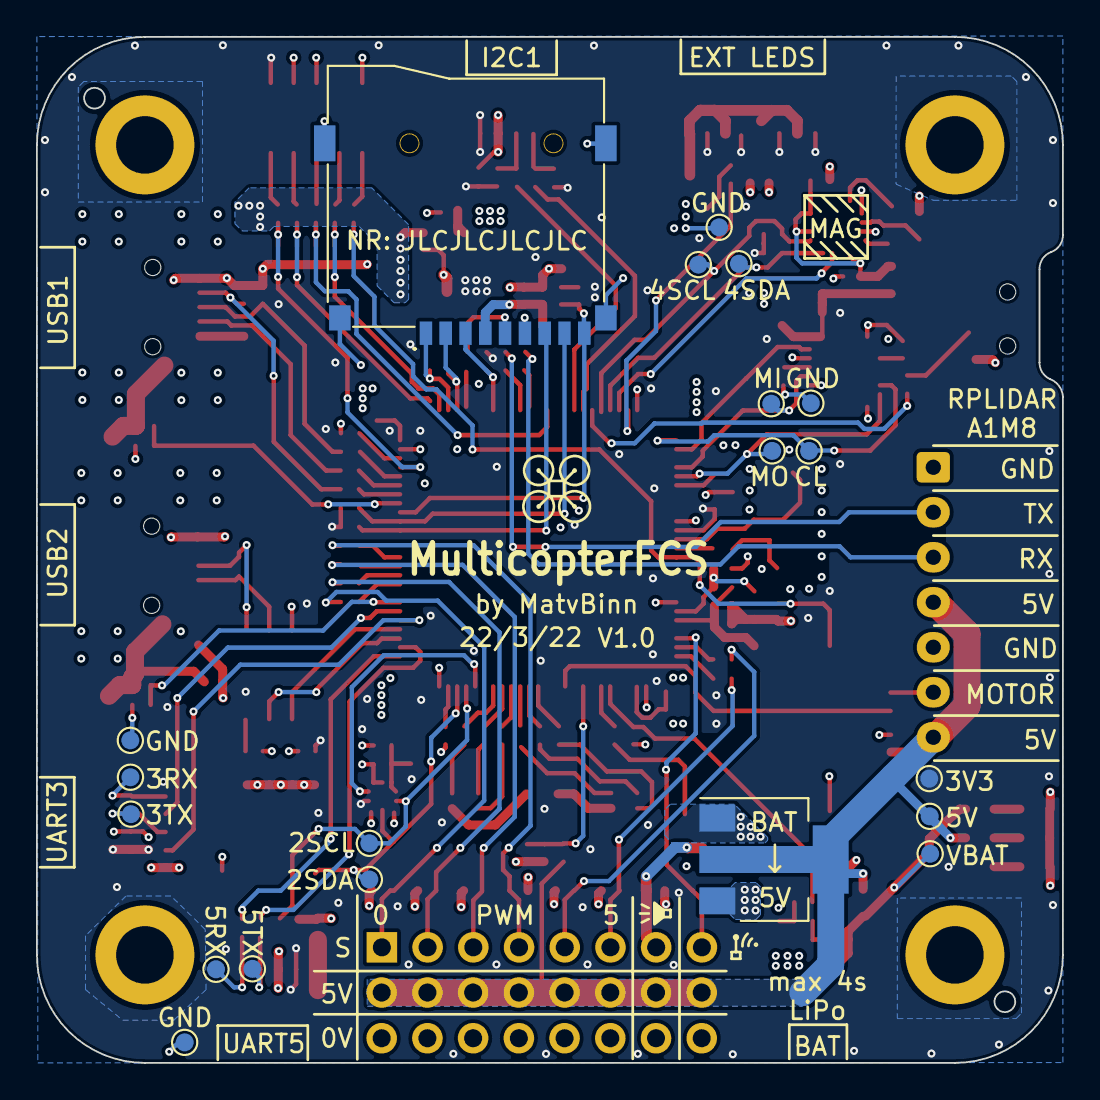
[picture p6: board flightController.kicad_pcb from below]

Board: 4 copper layers, 57.0 x 57.0 mm, 199 parts (20 on the bottom side), 125 nets.

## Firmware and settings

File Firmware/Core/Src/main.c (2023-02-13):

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
/* Includes ------------------------------------------------------------------*/
#include "main.h"
#include "cmsis_os.h"

/* USER CODE BEGIN Includes */

#include "MPU6000.h"

/* USER CODE END Includes */

ADC_HandleTypeDef hadc1;

I2C_HandleTypeDef hi2c1;
I2C_HandleTypeDef hi2c2;
I2C_HandleTypeDef hi2c4;

SPI_HandleTypeDef hspi4;
DMA_HandleTypeDef hdma_spi4_rx;

TIM_HandleTypeDef htim3;
TIM_HandleTypeDef htim4;
TIM_HandleTypeDef htim5;

UART_HandleTypeDef huart4;
UART_HandleTypeDef huart5;
UART_HandleTypeDef huart1;
UART_HandleTypeDef huart2;
UART_HandleTypeDef huart3;

osThreadId BlinkLED1Handle;
void SystemClock_Config(void);
void PeriphCommonClock_Config(void);
static void MX_GPIO_Init(void);
static void MX_I2C1_Init(void);
static void MX_I2C2_Init(void);
static void MX_TIM4_Init(void);
static void MX_TIM5_Init(void);
static void MX_USART1_UART_Init(void);
static void MX_USB_OTG_FS_USB_Init(void);
static void MX_UART4_Init(void);
static void MX_USART2_UART_Init(void);
static void MX_USART3_UART_Init(void);
static void MX_UART5_Init(void);
static void MX_I2C4_Init(void);
static void MX_ADC1_Init(void);
static void MX_TIM3_Init(void);
static void MX_DMA_Init(void);
static void MX_SPI4_Init(void);
void StartBlinkLED1(void const * argument);

/**
  * @brief  The application entry point.
  * @retval int
  */
int main(void)
{
  /* MCU Configuration--------------------------------------------------------*/

  /* Reset of all peripherals, Initializes the Flash interface and the Systick. */
  HAL_Init();

  /* Configure the system clock */
  SystemClock_Config();

/* Configure the peripherals common clocks */
  PeriphCommonClock_Config();

  /* Initialize all configured peripherals */
  MX_GPIO_Init();
  MX_I2C1_Init();
  MX_I2C2_Init();
  MX_TIM4_Init();
  MX_TIM5_Init();
  MX_USART1_UART_Init();
  MX_USB_OTG_FS_USB_Init();
  MX_UART4_Init();
  MX_USART2_UART_Init();
  MX_USART3_UART_Init();
  MX_UART5_Init();
  MX_I2C4_Init();
  MX_ADC1_Init();
  MX_TIM3_Init();
  MX_DMA_Init();
  MX_SPI4_Init();
  /* USER CODE BEGIN 2 */

  //MPU6000_init(&hspi4);

  /* USER CODE END 2 */

  /* USER CODE BEGIN RTOS_MUTEX */
  /* add mutexes, ... */
  /* USER CODE END RTOS_MUTEX */

  /* USER CODE BEGIN RTOS_SEMAPHORES */
  /* add semaphores, ... */
  /* USER CODE END RTOS_SEMAPHORES */

  /* USER CODE BEGIN RTOS_TIMERS */
  /* start timers, add new ones, ... */
  /* USER CODE END RTOS_TIMERS */

  /* USER CODE BEGIN RTOS_QUEUES */
  /* add queues, ... */
  /* USER CODE END RTOS_QUEUES */

  /* Create the thread(s) */
  /* definition and creation of BlinkLED1 */
  osThreadDef(BlinkLED1, StartBlinkLED1, osPriorityLow, 0, 128);
  BlinkLED1Handle = osThreadCreate(osThread(BlinkLED1), NULL);

  /* USER CODE BEGIN RTOS_THREADS */
  /* add threads, ... */
  /* USER CODE END RTOS_THREADS */

  /* Start scheduler */
  osKernelStart();

  /* We should never get here as control is now taken by the scheduler */
  /* Infinite loop */
  /* USER CODE BEGIN WHILE */
  while (1)
  {
    /* USER CODE END WHILE */

    /* USER CODE BEGIN 3 */
  }
  /* USER CODE END 3 */
}

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
/* USER CODE BEGIN Header_StartBlinkLED1 */
/**
  * @brief  Function implementing the BlinkLED1 thread.
  * @param  argument: Not used
  * @retval None
  */
/* USER CODE END Header_StartBlinkLED1 */
void StartBlinkLED1(void const * argument)
{
  /* USER CODE BEGIN 5 */
  // Setup for both Debug LEDs
  HAL_GPIO_WritePin(STATUS_LED1_R_GPIO_Port, STATUS_LED1_R_Pin, 1);
  HAL_GPIO_WritePin(STATUS_LED1_G_GPIO_Port, STATUS_LED1_G_Pin, 1);
  HAL_GPIO_WritePin(STATUS_LED1_B_GPIO_Port, STATUS_LED1_B_Pin, 1);
  HAL_GPIO_WritePin(STATUS_LED2_R_GPIO_Port, STATUS_LED2_R_Pin, 1);
  HAL_GPIO_WritePin(STATUS_LED2_G_GPIO_Port, STATUS_LED2_G_Pin, 1);
  HAL_GPIO_WritePin(STATUS_LED2_B_GPIO_Port, STATUS_LED2_B_Pin, 1);

  // Infinite loop
  for(;;)
  {
	// Blue
	HAL_GPIO_TogglePin(STATUS_LED1_B_GPIO_Port, STATUS_LED1_B_Pin);
	osDelay(500);
	HAL_GPIO_TogglePin(STATUS_LED1_B_GPIO_Port, STATUS_LED1_B_Pin);
	// Red
	HAL_GPIO_TogglePin(STATUS_LED1_R_GPIO_Port, STATUS_LED1_R_Pin);
	osDelay(500);
	HAL_GPIO_TogglePin(STATUS_LED1_R_GPIO_Port, STATUS_LED1_R_Pin);
	// Green
	HAL_GPIO_TogglePin(STATUS_LED1_G_GPIO_Port, STATUS_LED1_G_Pin);
	osDelay(500);
	HAL_GPIO_TogglePin(STATUS_LED1_G_GPIO_Port, STATUS_LED1_G_Pin);
  }

  osThreadTerminate(NULL); // Good practice to add for if you somehow exit the loop

  /* USER CODE END 5 */
}

/**
  * @brief  Period elapsed callback in non blocking mode
  * @note   This function is called  when TIM7 interrupt took place, inside
  * HAL_TIM_IRQHandler(). It makes a direct call to HAL_IncTick() to increment
  * a global variable "uwTick" used as application time base.
  * @param  htim : TIM handle
  * @retval None
  */
void HAL_TIM_PeriodElapsedCallback(TIM_HandleTypeDef *htim)
{
  if (htim->Instance == TIM7) {
    HAL_IncTick();
  }
}

/**
  * @brief  This function is executed in case of error occurrence.
  * @retval None
  */
void Error_Handler(void)
{
  /* USER CODE BEGIN Error_Handler_Debug */
  /* User can add his own implementation to report the HAL error return state */
  __disable_irq();

  HAL_GPIO_WritePin(STATUS_LED1_R_GPIO_Port, STATUS_LED1_R_Pin, 1);
  HAL_GPIO_WritePin(STATUS_LED1_G_GPIO_Port, STATUS_LED1_G_Pin, 1);
  HAL_GPIO_WritePin(STATUS_LED1_B_GPIO_Port, STATUS_LED1_B_Pin, 1);
  HAL_GPIO_WritePin(STATUS_LED2_R_GPIO_Port, STATUS_LED2_R_Pin, 1);
  HAL_GPIO_WritePin(STATUS_LED2_G_GPIO_Port, STATUS_LED2_G_Pin, 1);
  HAL_GPIO_WritePin(STATUS_LED2_B_GPIO_Port, STATUS_LED2_B_Pin, 1);

  while (1)
  {
	  HAL_GPIO_TogglePin(STATUS_LED1_R_GPIO_Port, STATUS_LED1_R_Pin);
	  HAL_Delay(100);
	  /*Test*/
	  HAL_GPIO_TogglePin(STATUS_LED2_R_GPIO_Port, STATUS_LED2_R_Pin);
  }
  /* USER CODE END Error_Handler_Debug */
}

#ifdef  USE_FULL_ASSERT
/**
  * @brief  Reports the name of the source file and the source line number
  *         where the assert_param error has occurred.
  * @param  file: pointer to the source file name
  * @param  line: assert_param error line source number
  * @retval None
  */
void assert_failed(uint8_t *file, uint32_t line)
{
  /* USER CODE BEGIN 6 */
  /* User can add his own implementation to report the file name and line number,
     ex: printf("Wrong parameters value: file %s on line %d\r\n", file, line) */
  /* USER CODE END 6 */
}
#endif /* USE_FULL_ASSERT */

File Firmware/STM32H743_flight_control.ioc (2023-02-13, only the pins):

Mcu.UserName=STM32H743VITx
PA0.Signal=UART4_TX
PA1.Signal=UART4_RX
PA10.Signal=USB_OTG_FS_ID
PA11.Signal=USB_OTG_FS_DM
PA12.Signal=USB_OTG_FS_DP
PA2.Signal=S_TIM5_CH3
PA3.Signal=S_TIM5_CH4
PA6.Signal=ADCx_INP3
PA7.GPIO_Label=BUZZ_ON
PA7.Signal=GPIO_Output
PA8.GPIO_Label=SD_CARD_DETECT
PA8.Signal=GPIO_Input
PA9.Signal=USB_OTG_FS_VBUS
PB1.Signal=S_TIM3_CH4
PB10.Signal=I2C2_SCL
PB11.Signal=I2C2_SDA
PB12.Signal=UART5_RX
PB13.Signal=UART5_TX
PB14.Signal=USART1_TX
PB15.Signal=USART1_RX
PB6.Signal=I2C1_SCL
PB7.Signal=I2C1_SDA
PB8.Signal=I2C4_SCL
PB9.Signal=I2C4_SDA
PD10.GPIO_Label=USB_VBUS_DEBUG
PD10.Signal=GPIO_Input
PD12.Signal=S_TIM4_CH1
PD13.Signal=S_TIM4_CH2
PD14.Signal=S_TIM4_CH3
PD15.Signal=S_TIM4_CH4
PD5.Signal=USART2_TX
PD6.Signal=USART2_RX
PD8.Signal=USART3_TX
PD9.Signal=USART3_RX
PE0.GPIO_Label=MAG_INT
PE0.Signal=GPIO_Input
PE1.GPIO_Label=LED_EXT
PE1.Signal=GPIO_Output
PE10.GPIO_Label=STATUS_LED1_B
PE10.Signal=GPIO_Output
PE11.GPIO_Label=STATUS_LED2_R
PE11.Signal=GPIO_Output
PE12.GPIO_Label=STATUS_LED2_G
PE12.Signal=GPIO_Output
PE13.GPIO_Label=STATUS_LED2_B
PE13.Signal=GPIO_Output
PE15.GPIO_Label=PS_INT
PE15.Signal=GPIO_Input
PE2.Signal=SPI4_SCK
PE3.GPIO_Label=IMU_INT
PE3.Signal=GPIO_Input
PE5.Signal=SPI4_MISO
PE6.Signal=SPI4_MOSI
PE8.GPIO_Label=STATUS_LED1_R
PE8.Signal=GPIO_Output
PE9.GPIO_Label=STATUS_LED1_G
PE9.Signal=GPIO_Output

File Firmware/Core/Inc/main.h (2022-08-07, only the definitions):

#define IMU_INT_Pin GPIO_PIN_3
#define IMU_INT_GPIO_Port GPIOE
#define BUZZ_ON_Pin GPIO_PIN_7
#define BUZZ_ON_GPIO_Port GPIOA
#define STATUS_LED1_R_Pin GPIO_PIN_8
#define STATUS_LED1_R_GPIO_Port GPIOE
#define STATUS_LED1_G_Pin GPIO_PIN_9
#define STATUS_LED1_G_GPIO_Port GPIOE
#define STATUS_LED1_B_Pin GPIO_PIN_10
#define STATUS_LED1_B_GPIO_Port GPIOE
#define STATUS_LED2_R_Pin GPIO_PIN_11
#define STATUS_LED2_R_GPIO_Port GPIOE
#define STATUS_LED2_G_Pin GPIO_PIN_12
#define STATUS_LED2_G_GPIO_Port GPIOE
#define STATUS_LED2_B_Pin GPIO_PIN_13
#define STATUS_LED2_B_GPIO_Port GPIOE
#define PS_INT_Pin GPIO_PIN_15
#define PS_INT_GPIO_Port GPIOE
#define USB_VBUS_DEBUG_Pin GPIO_PIN_10
#define USB_VBUS_DEBUG_GPIO_Port GPIOD
#define SD_CARD_DETECT_Pin GPIO_PIN_8
#define SD_CARD_DETECT_GPIO_Port GPIOA
#define MAG_INT_Pin GPIO_PIN_0
#define MAG_INT_GPIO_Port GPIOE
#define LED_EXT_Pin GPIO_PIN_1
#define LED_EXT_GPIO_Port GPIOE

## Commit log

2022-02-16 Initial KiCad commit
    [Connectors.kicad_sch, MCU_and_Power.kicad_sch, Peripherals.kicad_sch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]
2022-02-18 added the bmp388 pressure sensor
    [Connectors.kicad_sch, MCU_and_Power.kicad_sch, Peripherals.kicad_sch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]
2022-02-18 added the bmp388 footprint
2022-02-19 changed MCU to STM32H743VIT6
    [MCU_and_Power.kicad_sch, Peripherals.kicad_sch, flightController.kicad_sch]
2022-02-20 Added some pin definitions and drivers for mcu communication
    [Connectors.kicad_sch, MCU_and_Power.kicad_sch, Peripherals.kicad_sch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]
2022-02-20 added a connector for the RPLIDAR A1
    [Connectors.kicad_sch]
2022-02-22 Added SPI driver
    [Connectors.kicad_sch]
2022-02-23 Changed max PPM ESC controlers from 8->6 to make room for a buzzer and IBUS connection
    [Connectors.kicad_sch, MCU_and_Power.kicad_sch, Peripherals.kicad_sch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]
2022-02-26 Added pinlables, added SD cardholder footprint, fixed VBUS connection, added termination resistors for high frequency signals, improved schematic layout
    [Connectors.kicad_sch, MCU_and_Power.kicad_sch, Peripherals.kicad_sch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]
2022-02-26 More pin definitions
    [Connectors.kicad_sch, MCU_and_Power.kicad_sch, flightController.kicad_sch]
2022-02-27 Added pullups, testpoints and more pin definitions
    [Connectors.kicad_sch, MCU_and_Power.kicad_sch, Peripherals.kicad_sch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]
2022-03-04 Switched some RX and TX pins
    [Connectors.kicad_sch, MCU_and_Power.kicad_sch, Peripherals.kicad_sch]
2022-03-10 Added a connector for 4 external LEDs
    [Connectors.kicad_sch, flightController.kicad_sch]
2022-03-12 Added more footprints
    [Connectors.kicad_sch, MCU_and_Power.kicad_sch, Peripherals.kicad_sch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]
2022-03-12 added all footprints and reorganized schematic
    [Connectors.kicad_sch, MCU_and_Power.kicad_sch, Peripherals.kicad_sch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]
2022-03-12 Fixed pullup connected to SDIO CLK
    [Connectors.kicad_sch, flightController.kicad_sch]
2022-03-12 Fixed pullup being a pulldown for SDIO CD, added SD test points
    [Connectors.kicad_sch, Peripherals.kicad_sch, flightController.kicad_sch]
2022-03-12 Added more current limiting resistors
    [Connectors.kicad_sch, MCU_and_Power.kicad_sch, flightController.kicad_sch]
2022-03-12 Changed supply voltage for CH330N 5V->3V3
    [Connectors.kicad_sch, MCU_and_Power.kicad_sch, flightController.kicad_sch]
2022-03-12 Added a missing connection between the BECs and the LDO, removed some duplicate ferrite bead filtering
    [Connectors.kicad_sch, MCU_and_Power.kicad_sch, Peripherals.kicad_sch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]
2022-03-13 Added more filtering for the BMP, small labeling changes
    [Connectors.kicad_sch, MCU_and_Power.kicad_sch, Peripherals.kicad_sch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]
2022-03-13 Fixed duplicate external LED driver
    [MCU_and_Power.kicad_sch, Peripherals.kicad_sch, flightController.kicad_sch]
2022-03-13 Added a footprint for an optional VBAT->5V regulator
    [Connectors.kicad_sch, MCU_and_Power.kicad_sch, Peripherals.kicad_sch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]
2022-03-18 Final schematic changes made, added some annotations
    [Connectors.kicad_sch, MCU_and_Power.kicad_sch, Peripherals.kicad_sch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]
2022-03-18 Fixed ERC errors
    [Connectors.kicad_sch, MCU_and_Power.kicad_sch, Peripherals.kicad_sch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]
2022-03-19 Made a general PCB layout
    [Connectors.kicad_sch, MCU_and_Power.kicad_sch, Peripherals.kicad_sch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]
2022-03-20 Outline, component placement and some traces complete
    [flightController.kicad_pcb]
2022-03-20 Almost finished all routing
    [Connectors.kicad_sch, MCU_and_Power.kicad_sch, Peripherals.kicad_sch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]
2022-03-20 Routing finished
    [Connectors.kicad_sch, Peripherals.kicad_sch, flightController.kicad_pcb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]
2022-03-21 Added labels
    [Peripherals.kicad_sch, flightController.kicad_pcb, flightController.kicad_sch]
2022-03-21 Layout optimizations
    [flightController.kicad_pcb]
2022-03-22 Some small trace and layout optimisation
    [Peripherals.kicad_sch, flightController.kicad_pcb, flightController.kicad_sch]
2022-03-22 Added a 5V sense line
    [MCU_and_Power.kicad_sch, Peripherals.kicad_sch, flightController.kicad_pcb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]
2022-03-23 Changed the 3.3V LDO to one that supports a lower Vin so sub 5V USB supplies are less likely to pose a problem
    [Connectors.kicad_sch, MCU_and_Power.kicad_sch, Peripherals.kicad_sch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]
2022-03-26 SWD was 1mm pitch and needed to be 1.27 mm
    [Connectors.kicad_sch, Peripherals.kicad_sch, flightController.kicad_pcb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]
2022-07-05 Last layout optimizations and checks before production
    [Connectors.kicad_sch, MCU_and_Power.kicad_sch, Peripherals.kicad_sch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]
2022-07-11 Updated BOM table
    [flightController.kicad_pcb]
2022-07-12 Finalizing V1.0 PCB, design send off for production
    [Connectors.kicad_sch, MCU_and_Power.kicad_sch, Peripherals.kicad_sch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]
2022-07-31 Added a basic Firmware setup for the MCU in the CubeIDE
    [flightController.kicad_pcb]
2022-08-07 LED blink
2022-08-07 LED indicator colour cycle for testing
2022-08-07 Changed some of the LED resistor values to make the red channel less dim
    [Connectors.kicad_sch, Peripherals.kicad_sch, flightController.kicad_sch]
2022-08-12 Added c files for al peripherals, attempted to get the MCU to communicate over SPI but no succes
    [Connectors.kicad_sch, MCU_and_Power.kicad_sch, Peripherals.kicad_sch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]
2023-02-13 Added a folder for the Matlab test scripts and added some test drivers
    [Peripherals.kicad_sch]

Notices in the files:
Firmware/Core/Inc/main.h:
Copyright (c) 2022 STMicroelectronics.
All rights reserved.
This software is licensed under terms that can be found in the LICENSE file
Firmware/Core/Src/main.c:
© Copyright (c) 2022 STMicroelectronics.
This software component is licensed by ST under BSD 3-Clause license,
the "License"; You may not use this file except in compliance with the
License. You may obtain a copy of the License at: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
